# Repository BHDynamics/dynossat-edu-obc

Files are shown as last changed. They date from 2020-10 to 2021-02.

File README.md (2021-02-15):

# DynOSSAT-EDU-OBC (On-Board Computer)

**Important note: we have updated the Arduino Boards Manager link.** Please update your Arduino IDE settings with our new link: https://bhdynamics.github.io/board_index/package_bhdynamics_index.json since the previous one (https://bhdynamics.github.io/board_index/package_dynossat_index.json) **NO LONGER WORKS**.

DynOSSAT-EDU is the first open source PocketQube educational kit compatible with CircuitPython and Arduino.

This plaform is equipped with all the necessary modules for the operation of a nanosatellite (PocketQube)
in Low Earth Orbit (LEO) that would serve as a device for teaching, training, and driving curiosity about the philosophy and technology related to NewSpace.

This repository contains the hardware files for the OBC (On-Board Computer), the module responsible for managing the satellite and process sensor data. It
integrates a 9-axis IMU and carries a powerful ATSAMD51.

Hardware in this repository is licenced under **CERN OHL v1.2**.

## Technical details

- Powerful ATSAMD51J20A-AU 120 MHz Cortex-M4F processor with 1 MB flash + 256 KB RAM for all your CircuitPython needs
- 32 Mbit SPI flash for storing CircuitPython code and libraries
- High-precision ICM-20948 Inertial Measurement Unit including Accelerometer, Gyroscope and Magnetometer for Attitude management
- MCP9808 Digital Temperature Sensor
- SGP30 TVOC and eqCO2 air quality sensor
- User-controllable WS2812B addressable RGB LED
- Separate 5V and 3.3V rails, providing up to 1A/500mA respectively
- MicroSD Card slot
- Female USB-C 2.0 connector for power and data logging
- PQBH40 bus exposing 10 digital pins, 6 analog pins (+ true DAC), an I2C bus, an SPI bus and an UART

## Documentation

Available in this repo's [Wiki](https://github.com/BHDynamics/dynossat-edu-obc/wiki).

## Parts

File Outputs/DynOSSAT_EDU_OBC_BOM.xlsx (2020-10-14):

Item | Qty | Reference(s) | Value | Part Number | Comments
1 | 4 | C1, C3, C6, C17 | 10uF |  | 0603 10uF X7R/X5R 10V or greater
2 | 11 | C2, C8, C11, C12, C13, C14, C15, C16, C18, C19, C20 | 100nF |  | 0402 100nF X7R/X5R 10V or greater
3 | 2 | C4, C5 | 22pF |  | 0402 22pF NP0/C0G
4 | 2 | C7, C9 | 4.7uF |  | 0402 4.7uF X7R/X5R 6.3V or greater
5 | 1 | C10 | 1uF |  | 0402 1uF X7R/X5R 10V or greater
6 | 1 | D2 | Red |  | 0603 LED Red
7 | 1 | D3 | WS2812B | WS2812B-MINI | RGB LED
8 | 1 | J1 | Main Bus PQBH40 | We don't have part numbers. Use generic connectors | Pin header male 1.27mm pitch 2x20 vertical SMD
9 | 1 | J2 | Main Bus PQBH40 | We don't have part numbers. Use generic connectors | Pin socket female 1.27mm pitch 2x20 vertical SMD
10 | 1 | J3 | Micro_SD_Card | TF-102-18 | Micro SD Card Holder
11 | 1 | J4 | USB_C_Receptacle_USB2.0 | U262-161N-4BVC11 | USB-C 2.0 connector - female socket
12 | 2 | Q1, Q2 | BSS138 | BSS138 | N-Channel MOSFET
13 | 2 | Q3, Q4 | DMG2305L | DMG2305UX-7 | P-Channel Power Mosfet
14 | 3 | R1, R6, R13 | 100k |  | 0402 100k 1%
15 | 2 | R2, R3 | 5.1k |  | 0402 5.1k 1%
16 | 2 | R4, R5 | 10k |  | 0402 10k 1%
17 | 2 | R7, R8 | 510R |  | 0402 510R 1%
18 | 4 | R9, R10, R11, R12 | 10k |  | 0402 10k 1%
19 | 1 | SW1 | RESET | 1TS002G-1800-3500-CT | Push Button side mount
20 | 1 | U1 | GD25Q32 | GD25Q32CNIGR | 32 Mbit flash memory SPI
21 | 1 | U2 | ME6211C33 | ME6211C33M5G-N | 3V3 LDO SOT-23-5
22 | 1 | U3 | ME6211C | ME6211C18M5G-N | 1V8 LDO SOT-23-5
23 | 1 | U5 | ICM-20948 | ICM-20948 | Inertial Measurement Unit
24 | 1 | U6 | SGP30 | SGP30-2.5k | VOC & eCO2 Gas Sensor
25 | 1 | U7 | MCP9808 | MCP9808T-E/MS | Package_SO:MSOP-8_3x3mm_P0.65mm
26 | 1 | U8 | ATSAMD51J20A-AU | ATSAMD51J20A-AU | MCU TQFP64
27 | 1 | Y1 | 32.768k - 12.5pF | X201232768KGD2SI | 2012 32768 kHz Crystal 12.5pF
For passives (resistors, capacitors, etc) you may use any quality brand while meeting requirements

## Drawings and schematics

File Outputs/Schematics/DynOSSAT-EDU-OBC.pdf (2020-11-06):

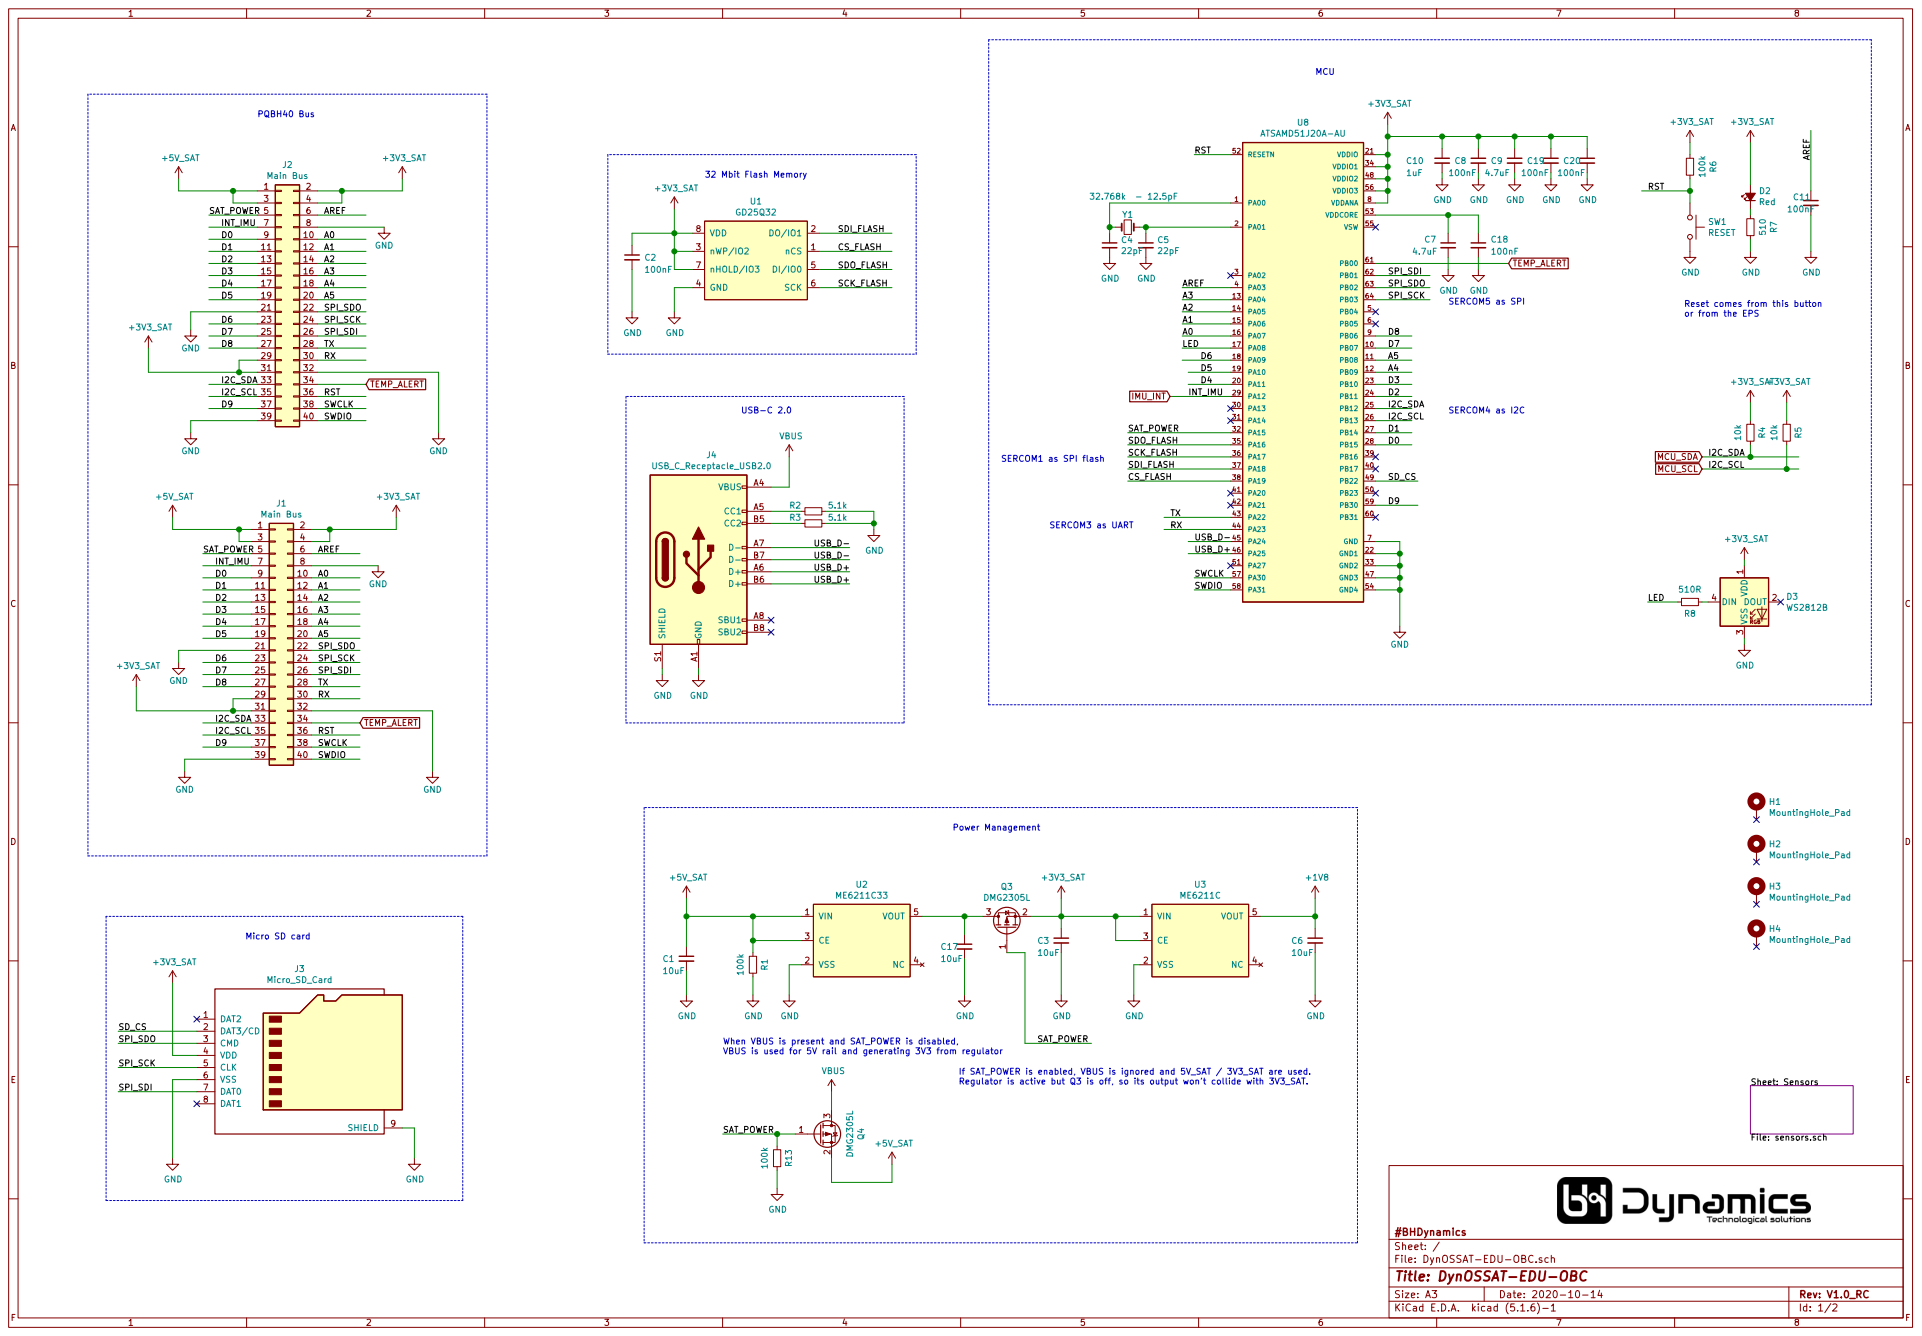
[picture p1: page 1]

SERCOM5 as SPI SERCOM1 as SPI flash

Reset comes from this button

or from the EPS USB-C 2.0

When VBUS is present and SAT_POWER is disabled,
VBUS is used for 5V rail and generating 3V3 from regulator

If SAT_POWER is enabled, VBUS is ignored and 5V_SAT / 3V3_SAT are used.
Regulator is active but Q3 is off, so its output won't collide with 3V3_SAT.

Id: 1/2 Title: DynOSSAT-EDU-OBC

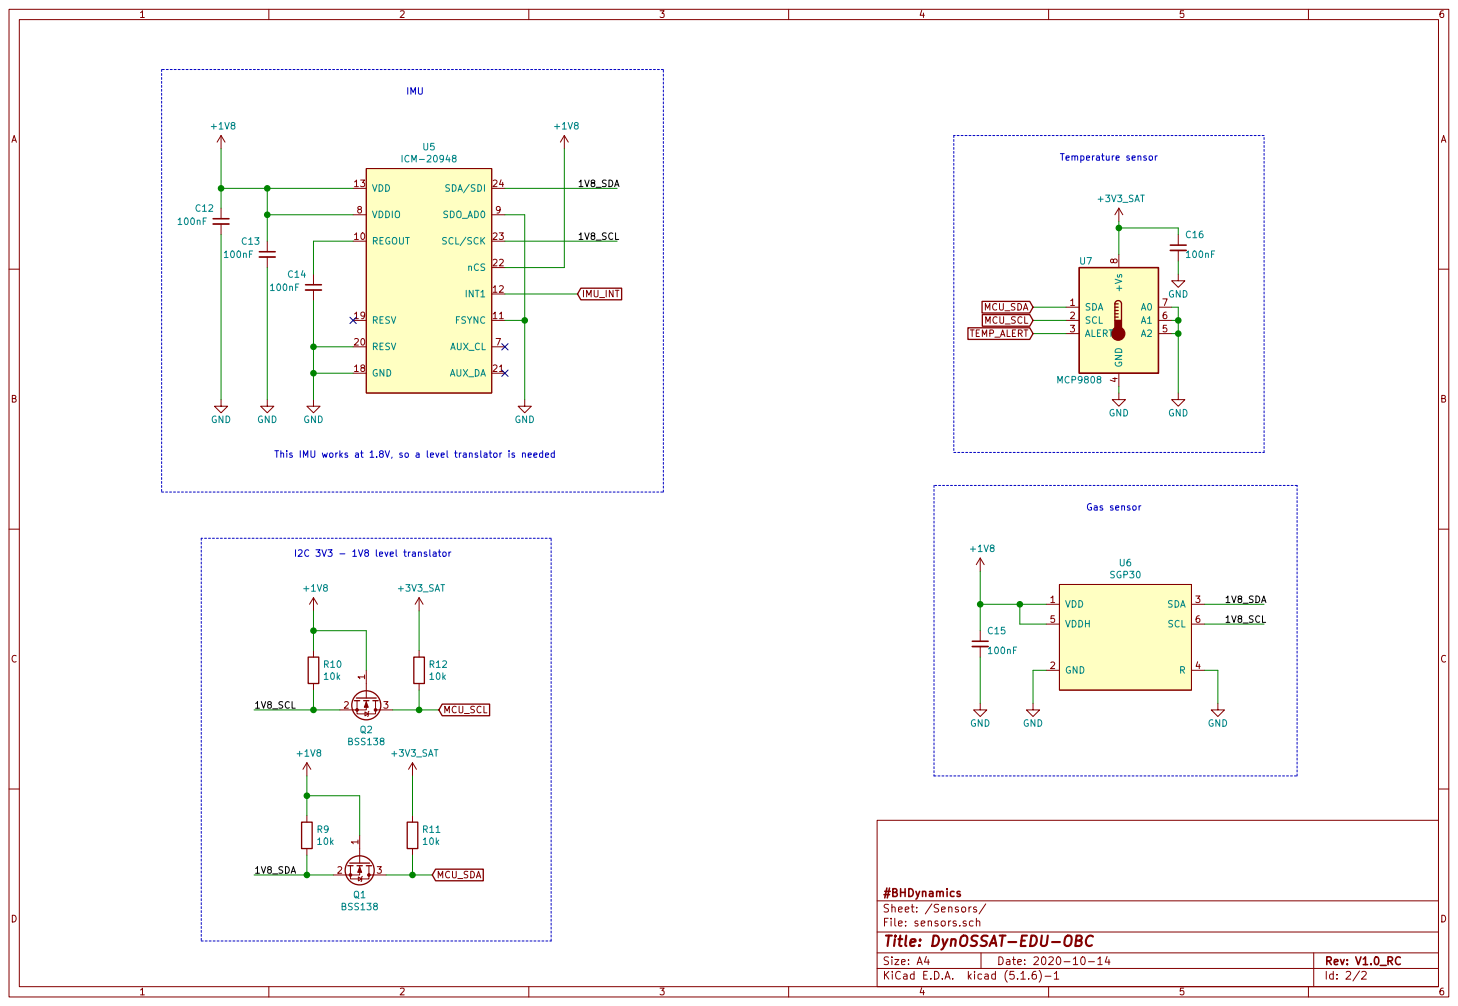
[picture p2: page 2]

Temperature sensor Gas sensor

This IMU works at 1.8V, so a level translator is needed

File: sensors.sch Sheet: /Sensors/ #BHDynamics

Id: 2/2 Title: DynOSSAT-EDU-OBC

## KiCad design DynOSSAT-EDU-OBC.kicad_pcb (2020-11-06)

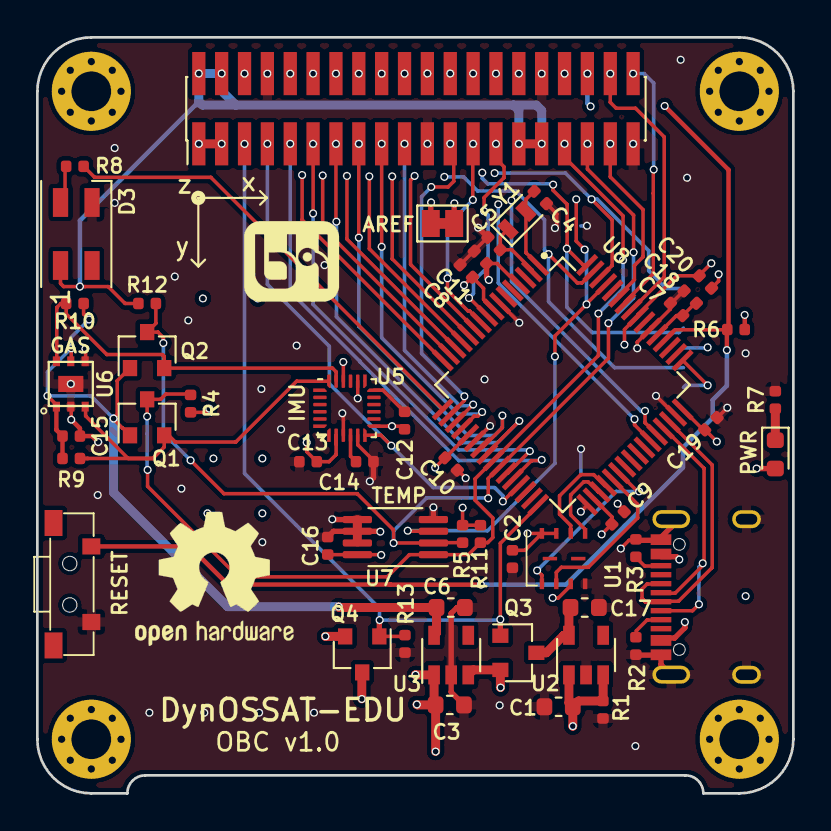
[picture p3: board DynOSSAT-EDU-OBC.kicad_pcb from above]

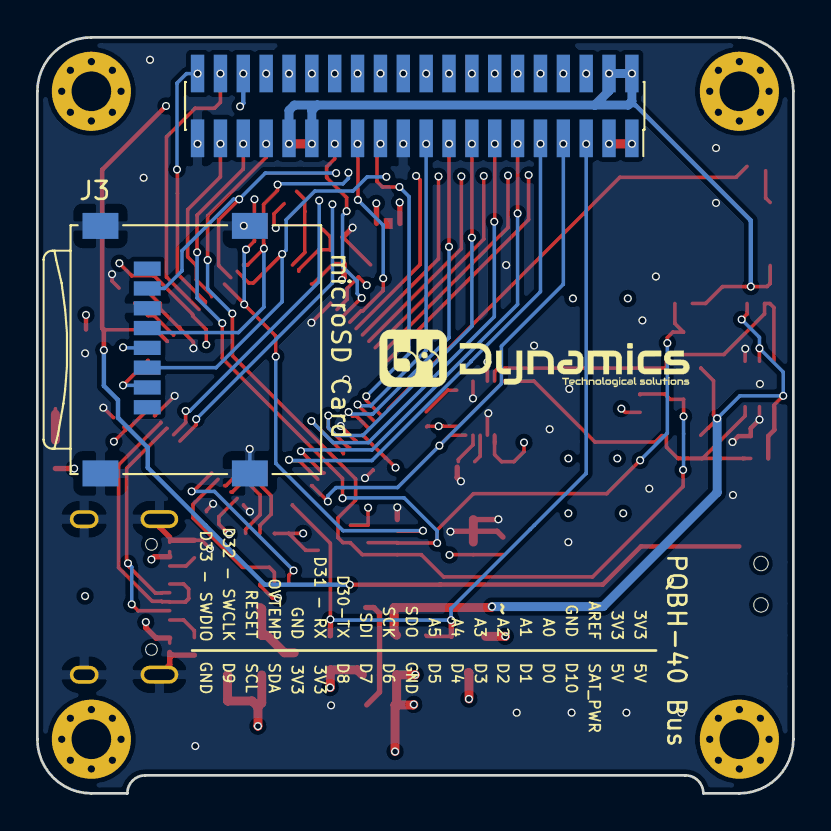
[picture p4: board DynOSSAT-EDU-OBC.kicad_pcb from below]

Board: 4 copper layers, 42.0 x 42.0 mm, 57 parts (2 on the bottom side), 54 nets.

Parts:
C1, C3, C6, C17: 10uF; C_0603_1608Metric
C2, C8, C11, C12, C13, C14, C15, C16, C18, C19, C20: 100nF; C_0402_1005Metric
C4, C5: 22pF; C_0402_1005Metric
C7, C9: 4.7uF; C_0402_1005Metric
C10: 1uF; C_0402_1005Metric
D2: Red; LED_0603_1608Metric
D3: WS2812B; LED_SK6812MINI_PLCC4_3.5x3.5mm_P1.75mm
H1, H2, H3, H4: MountingHole_Pad; MountingHole_2.2mm_M2_Pad_Via
J1: Main Bus; PinHeader_2x20_P1.27mm_Vertical_SMD
J2: Main Bus; PinSocket_2x20_P1.27mm_Vertical_SMD
J3: Micro_SD_Card; TF-102-18
J4: USB_C_Receptacle_USB2.0; U262-161N-4BVC11
JP2: Jumper; SolderJumper-2_P1.3mm_Bridged_Pad1.0x1.5mm
Q1, Q2: BSS138; SOT-23
Q3, Q4: DMG2305L; SOT-23
R1, R6, R13: 100k; R_0402_1005Metric
R2, R3: 5.1k; R_0402_1005Metric
R4, R5, R9, R10, R11, R12: 10k; R_0402_1005Metric
R7: 510; R_0402_1005Metric
R8: 510R; R_0402_1005Metric
SW1: RESET; 1TS002G-1800-3500-CT
U1: GD25Q32; WSON-8-1EP_3x4mm_P0.8mm
U2: ME6211C33; SOT-23-5
U3: ME6211C; SOT-23-5
U5: ICM-20948; QFN-24-1EP_3x3mm_P0.4mm_EP1.75x1.6mm
U6: SGP30
U7: MCP9808; MSOP-8_3x3mm_P0.65mm
U8: ATSAMD51J20A-AU; QFP50P1200X1200X120-64N
Y1: 32.768k - 12.5pF; Crystal_SMD_2012-2Pin_2.0x1.2mm

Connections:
+1V8: C6.1, C12.1, C13.1, C15.1, Q1.1, Q2.1, R9.1, R10.1, U3.5, U5.8, U5.13, U5.22, U6.1, U6.5
+3V3_SAT: C2.1, C3.1, C8.1, C9.1, C10.1, C16.1, C19.1, C20.1, D2.2, D3.1, J1.2, J1.4, J1.29, J1.31, J2.2, J2.4, J2.29, J2.31, J3.4, JP2.1, Q3.2, R4.2, R5.2, R6.2, R11.1, R12.1, U1.3, U1.7, U1.8, U3.1, U3.3, U7.8, U8.8, U8.21, U8.34, U8.48, U8.56
+5V_SAT: C1.1, J1.1, J1.3, J2.1, J2.3, Q4.2, R1.2, U2.1, U2.3
/A0: J1.10, J2.10, U8.16
/A1: J1.12, J2.12, U8.15
/A2: J1.14, J2.14, U8.14
/A3: J1.16, J2.16, U8.13
/A4: J1.18, J2.18, U8.12
/A5: J1.20, J2.20, U8.11
/AREF: C11.1, J1.6, J2.6, JP2.2, U8.4
/CS_FLASH: U1.1, U8.38
/D0: J1.9, J2.9, U8.28
/D1: J1.11, J2.11, U8.27
/D2: J1.13, J2.13, U8.24
/D3: J1.15, J2.15, U8.23
/D4: J1.17, J2.17, U8.20
/D5: J1.19, J2.19, U8.19
/D6: J1.23, J2.23, U8.18
/D7: J1.25, J2.25, U8.10
/D8: J1.27, J2.27, U8.9
/D9: J1.37, J2.37, U8.59
/LED: R8.1, U8.17
/RST: J1.36, J2.36, R6.1, SW1.1, U8.52
/RX: J1.30, J2.30, U8.44
/SAT_POWER: J1.5, J2.5, Q3.1, Q4.1, R13.2, U8.32
/SCK_FLASH: U1.6, U8.36
/SDI_FLASH: U1.2, U8.37
/SDO_FLASH: U1.5, U8.35
/SD_CS: J3.2, U8.49
/SPI_SCK: J1.24, J2.24, J3.5, U8.64
/SPI_SDI: J1.26, J2.26, J3.7, U8.62
/SPI_SDO: J1.22, J2.22, J3.3, U8.63
/SWCLK: J1.38, J2.38, U8.57
/SWDIO: J1.40, J2.40, U8.58
/Sensors/1V8_SCL: Q2.2, R10.2, U5.23, U6.6
/Sensors/1V8_SDA: Q1.2, R9.2, U5.24, U6.3
/TX: J1.28, J2.28, U8.43
/USB_D+: J4.A6, J4.B6, U8.46
/USB_D-: J4.A7, J4.B7, U8.45
GND: C1.2, C2.2, C3.2, C4.2, C5.2, C6.2, C7.2, C8.2, C9.2, C10.2, C11.2, C12.2, C13.2, C14.2, C15.2, C16.2, C17.2, C18.2, C19.2, C20.2, D3.3, J1.8, J1.21, J1.32, J1.39, J2.8, J2.21, J2.32, J2.39, J3.6, J3.9, J4.A1, J4.A12, J4.B1, J4.B12, J4.S1, R1.1, R2.1, R3.1, R7.1, R13.1, SW1.2, U1.4, U2.2, U3.2, U5.9, U5.11, U5.18, U5.20, U6.2, U6.4, U6.P$7, U7.4, U7.5, U7.6, U7.7, U8.7, U8.22, U8.33, U8.47, U8.54
IMU_INT: J1.7, J2.7, U5.12, U8.29
MCU_SCL: J1.35, J2.35, Q2.3, R5.1, R12.2, U7.2, U8.26
MCU_SDA: J1.33, J2.33, Q1.3, R4.1, R11.2, U7.1, U8.25
unnamed: C4.1, U8.1, Y1.2
unnamed: C5.1, U8.2, Y1.1
unnamed: C14.1, U5.10
unnamed: C17.1, Q3.3, U2.5
unnamed: C7.1, C18.1, U8.53
unnamed: D2.1, R7.2
unnamed: D3.4, R8.2
unnamed: J4.A5, R2.2
unnamed: J4.B5, R3.2
TEMP_ALERT: J1.34, J2.34, U7.3, U8.61
VBUS: J4.A4, J4.A9, J4.B4, J4.B9, Q4.3

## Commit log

2020-10-14 First commit, RC1.0
    [DynOSSAT-EDU-OBC-B_Cu.gbr, DynOSSAT-EDU-OBC-B_Fab.gbr, DynOSSAT-EDU-OBC-B_Mask.gbr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]
2020-10-19 Update 3D models on MCU and button footprints
    [DynOSSAT-EDU-OBC.kicad_pcb]
2020-11-06 Change MISO/MOSI for SDI/SDO
    [DynOSSAT-EDU-OBC-B_Cu.gbr, DynOSSAT-EDU-OBC-B_Fab.gbr, DynOSSAT-EDU-OBC-B_Mask.gbr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]
